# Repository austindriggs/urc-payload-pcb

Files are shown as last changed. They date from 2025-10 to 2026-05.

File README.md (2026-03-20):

# Payload PCB at WVU for Mars Society's University Rover Challenge (URC)







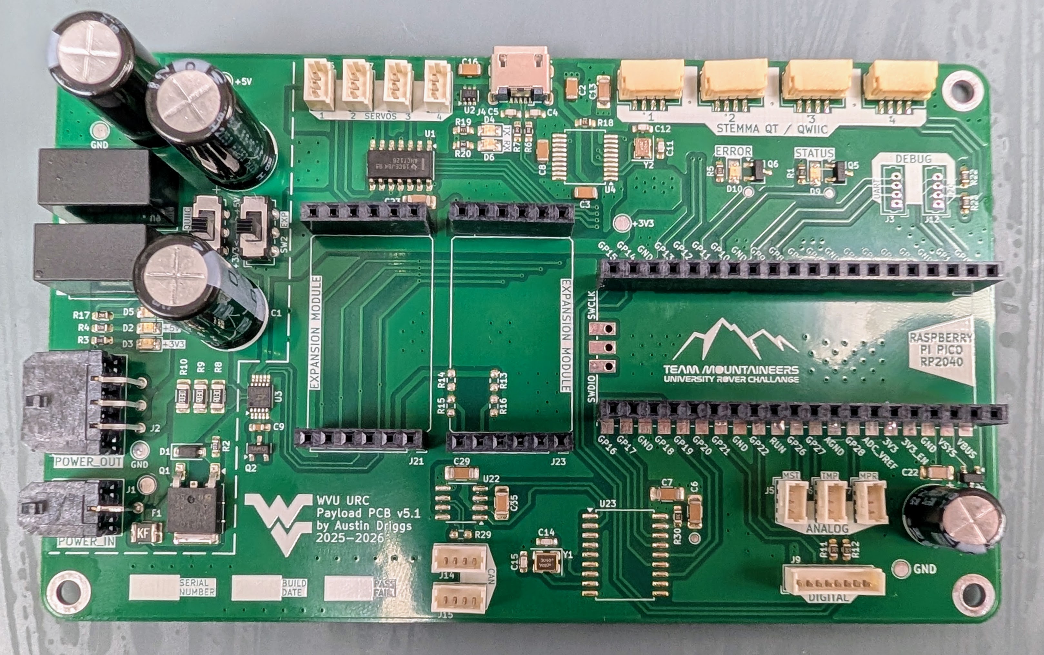
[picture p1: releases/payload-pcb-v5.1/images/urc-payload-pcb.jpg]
urc-payload-pcb


## SUMMARY

The Payload PCB serves as an all-purpose control and interface board that contains the Raspberry Pi Pico (RP2040) designed to manage mission-critical sensors and electronics and communicate that information through its Micro USB connector to the LattePanda Sigma SBC.

Learn how to [contribute](CONTRIBUTING.md) (with pictures) to this project.

## FEATURES

- Resettable PTC fuse and reverse voltage protection on +12V Molex Micro-Fit input.
- LTC2990 Quad I2C Voltage, Current, and Temperature Monitor.
- Traco TSR 2 Series +5V and +3V3 regulators: 96% eff, no heat sink required, built in filter caps, and short circuit protection.
- Outputs +12V, +5V, and +3V3 on Molex Micro-Fit.
- Status and error LEDs.
- Connections for both the Pico and an external device to CAN bus.
- 4x STEMMA QT / QWIIC connectors for COTS modules and peripherals.
- 2x custom expansion modules on two 6 pin 0.1" connectors each.
- 4x servo (PWM) outputs on Molex PicoBlades.
- 3x analog inputs on Molex Picoblades.
- 2x digital outputs for relays.
- 2x digital inputs (active-low) for limit switches on manipulator linear rail.
- Micro USB port with soft start to connect to Seeeduino XIAO on manipulator.

## DESIGN

<!--
### SCHEMATIC

TODO

### LAYOUT
--->

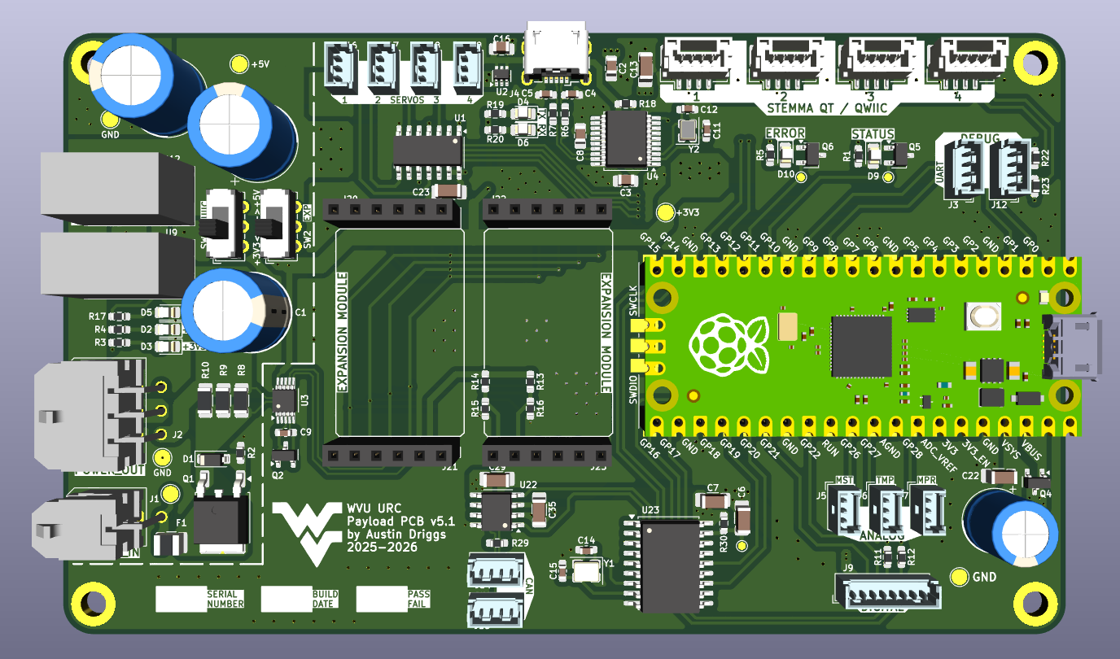
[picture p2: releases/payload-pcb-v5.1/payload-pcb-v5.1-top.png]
top


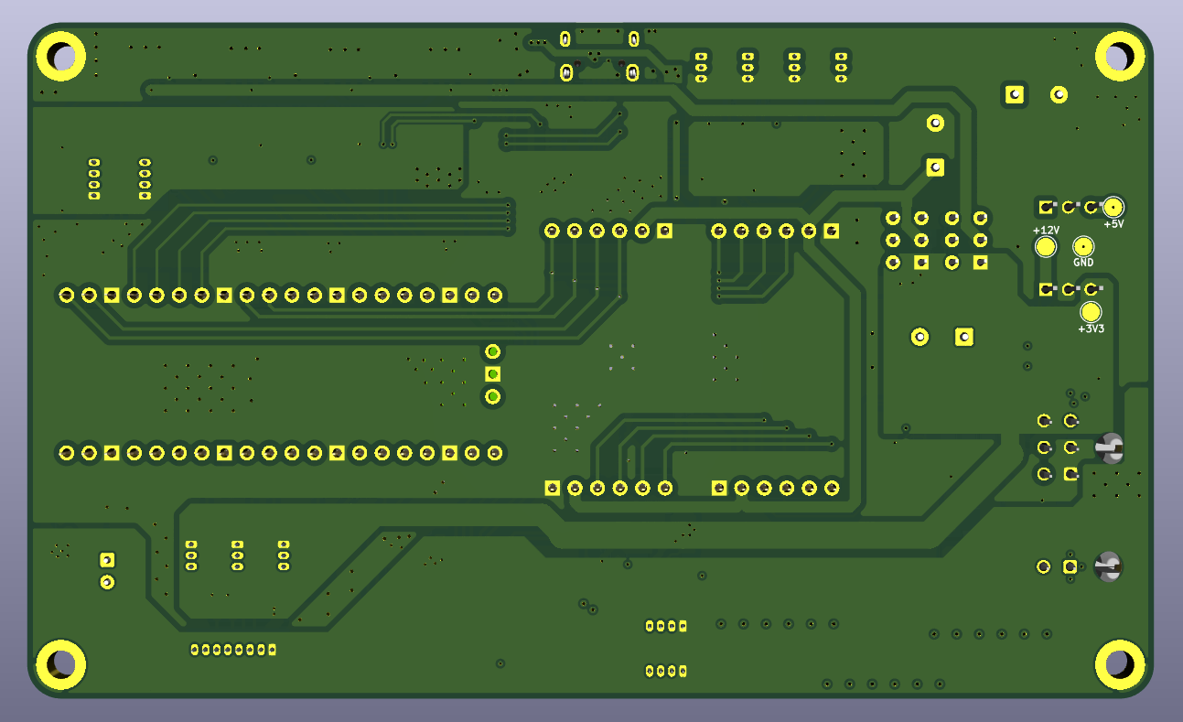
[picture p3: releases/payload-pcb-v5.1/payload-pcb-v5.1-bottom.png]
bottom


<!--
### MODEL

TODO
--->

## DEIMOS (ROVER) AND PHOBOS (DRONE) FOR 2026

Click the image below to watch the System Acceptance Review (SAR) on YouTube:  
<a href="https://youtu.be/ZTezlA8RuXI?si=s-GYmmxkBqftyrRB" target="_blank">
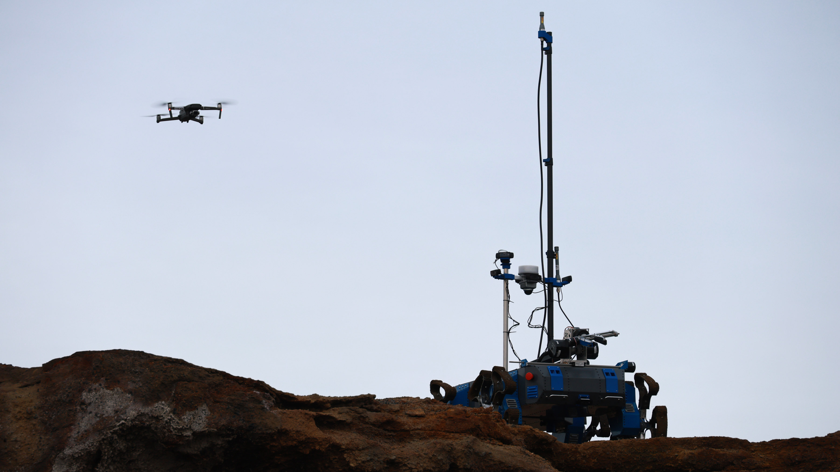
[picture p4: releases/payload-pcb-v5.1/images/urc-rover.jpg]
URC Rover Video
  
</a>

## LICENSE

This project is published under the MIT [license](LICENSE).

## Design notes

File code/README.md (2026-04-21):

# pico_interface_pkg

This package includes the code for both the node that needs to run on the Latte Panda to communicate with the pico as well as the code that needs to be flashed onto the pico.

The code on the pico itself has a simple overall function. It will poll its serial port, take in a message, and then decode that message and exectute an action based on its contents.

## starting

```bash
ros2 run pico_interface_pkg pico_host_node
```

## pico_science_node.py - (All Pico Code For Deimos)

Commands to run Linear Actuator on Manipulator

extend
```bash
ros2 topic pub --once /science/actuator_pos robot_interfaces/msg/STargetedFloat "{target: 'act', data: 1.0}"
```

retract
```bash
ros2 topic pub --once /science/actuator_pos robot_interfaces/msg/STargetedFloat "{target: 'act', data: 0.0}"
```

stop
```bash
ros2 topic pub --once /science/actuator_pos robot_interfaces/msg/STargetedFloat "{target: 'act', data: 0.5}"
```

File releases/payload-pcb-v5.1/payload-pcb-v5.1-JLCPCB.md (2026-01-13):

# Payload PCB v5.1 JLCPCB

The bolded text are what needs changed, but everything should be verified. Last updated: 2025-01-13

## Online PCB Quote

1. Add gerbers from `releases/payload-pcb-v5.1/gerbers/payload-pcb-v5.1-gerbers.zip`
2. Base Material = FR-4
3. **Layers = 4**
4. **Dimensions = 5 * 3 inch**
5. **PCB Qty = 10**
6. Product Type = Industrial/Consumer electronics

## PCB Specifications

1. Different Design = 1
2. Delivery Format = Single PCB
3. PCB Thickness = 1.6mm
4. **PCB Color = Blue**
5. Silkscreen = White
6. Material Type = FR4 TG135
7. Surface Finish = HASL (with lead)

## High-spec Options

1. Outer Copper Weight = 1 oz
2. Inner Copper Weight = 0.5 oz
3. **Specify Layer Sequence = Yes**
	1. L1 = F_Cu
	2. L2 = GND1
	3. L3 = GND2
	4. L4 = B_Cu
4. Specify Stackup = No
5. Via Covering = Tented
6. Via Plating Method = Not Specified
7. Min via hole size/diameter = 0.3mm
8. Board Outline Tolerance = +-0.2mm
9. Confirm Production file = no
10. Mark on PCB = Remove Mark
11. Electrical Test = Flying Probe Fully Test
12. Gold Fingers = No
13. Castellated Holes = No
14. Edge Plating = No
15. Blind Slots = No
16. UL Marking = No
17. Backdrill = No

## Stencil

1. Framwork = No
2. Step Stencil = No
3. Nano-Coating = No
4. Stencil Side = Top only
5. Dimensions = Standard Size = 380 * 280
6. Stencil Qty = 1
7. **Thickness = Select by Customer = 0.12 mm**
8. Stencil Process Type = Solder paste stencil
9. **Polishing Process = Etching**
10. Fiducials = No Fiducial
11. Confirm Production file = No
12. **Engrave Text = Yes = payload-pcb-v5.1**
13. Package Box = With JLCPCB logo

# Estimated Cost

## Charge Details

- Engineering fee $24.00
- Via Covering $0.00
- Surface Finish $0.00
- Color $4.90
- Board $10.10
- Stencil $7.00
- Engrave Text $0.49
- Etching $3.22

## PCB Build Time

-  **3-4 days $0.00**
-  3 days PCBA Only $0.00
-  2-3 days $64.30

## Calculated Price

- $49.71

## Shipping Estimate 

- $43.67
- DHL Express (DDP) 2-4 business days
- Weight 1.42kg

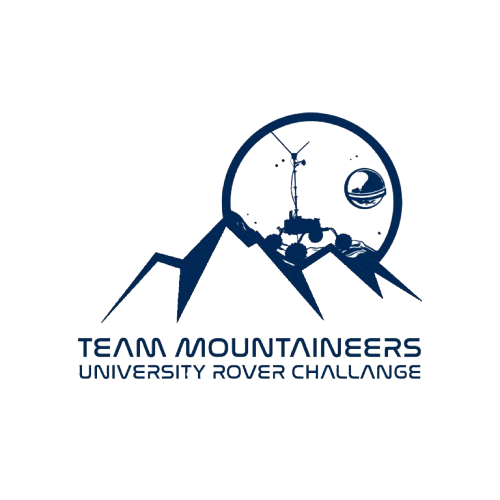
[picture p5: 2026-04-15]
support/Untitled design.png

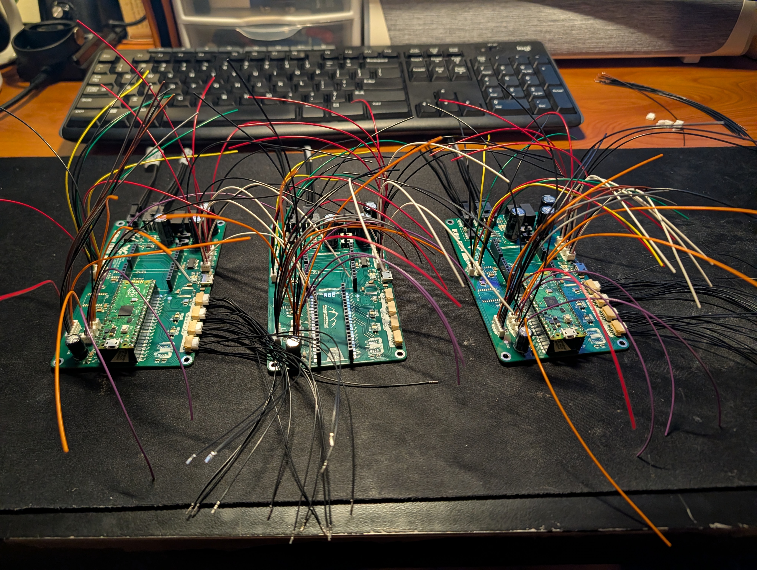
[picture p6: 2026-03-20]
releases/payload-pcb-v5.1/images/05-wired.jpg

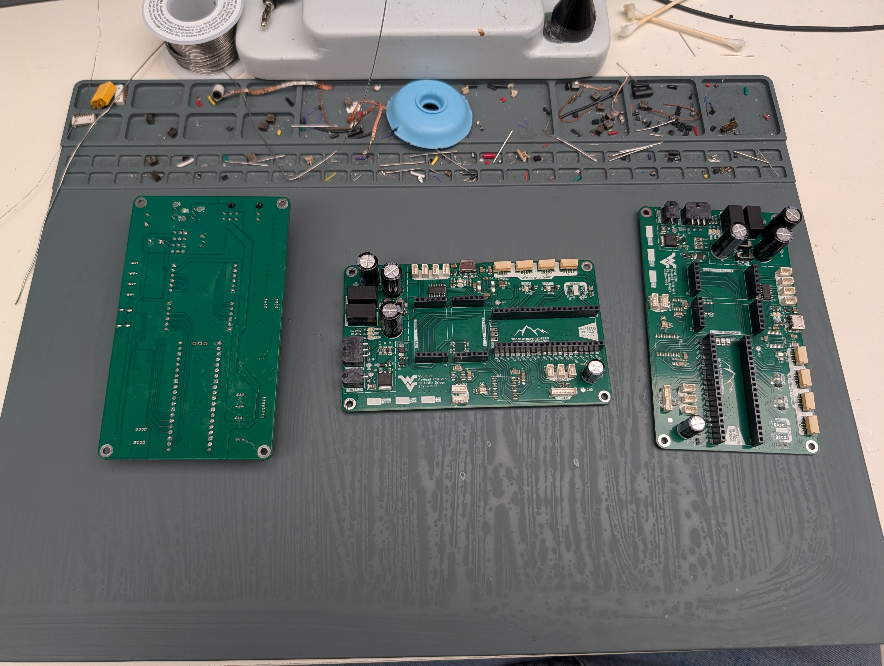
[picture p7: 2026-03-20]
releases/payload-pcb-v5.1/images/04-zoomed.jpg

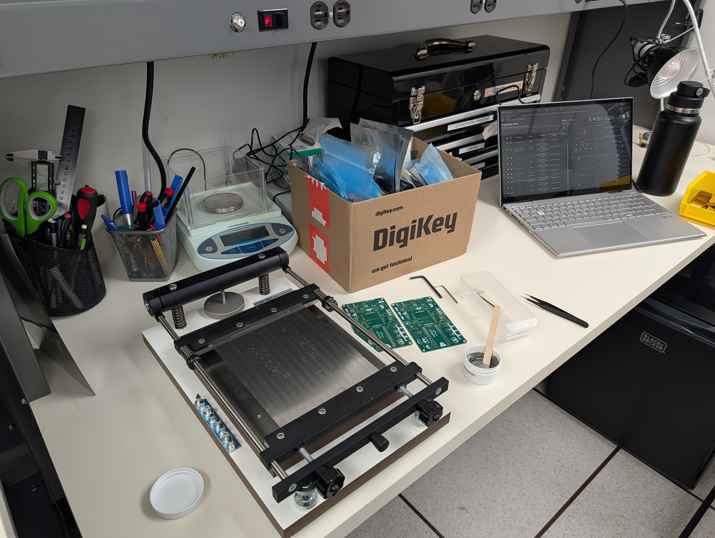
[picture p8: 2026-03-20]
releases/payload-pcb-v5.1/images/01-stencil.jpg

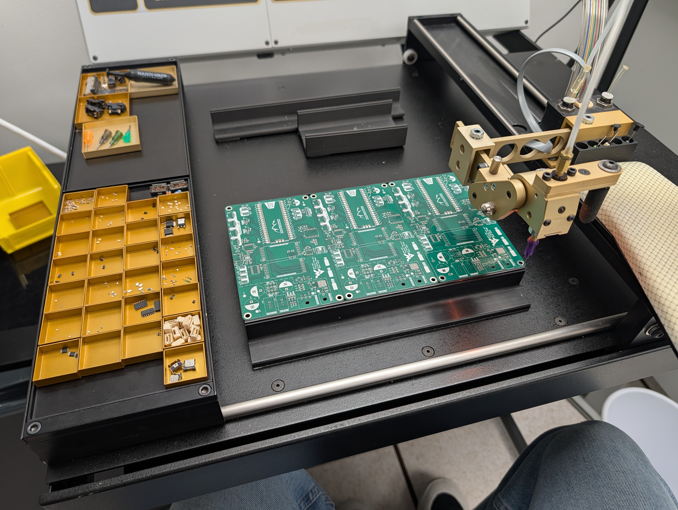
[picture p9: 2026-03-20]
releases/payload-pcb-v5.1/images/02-wiped.jpg

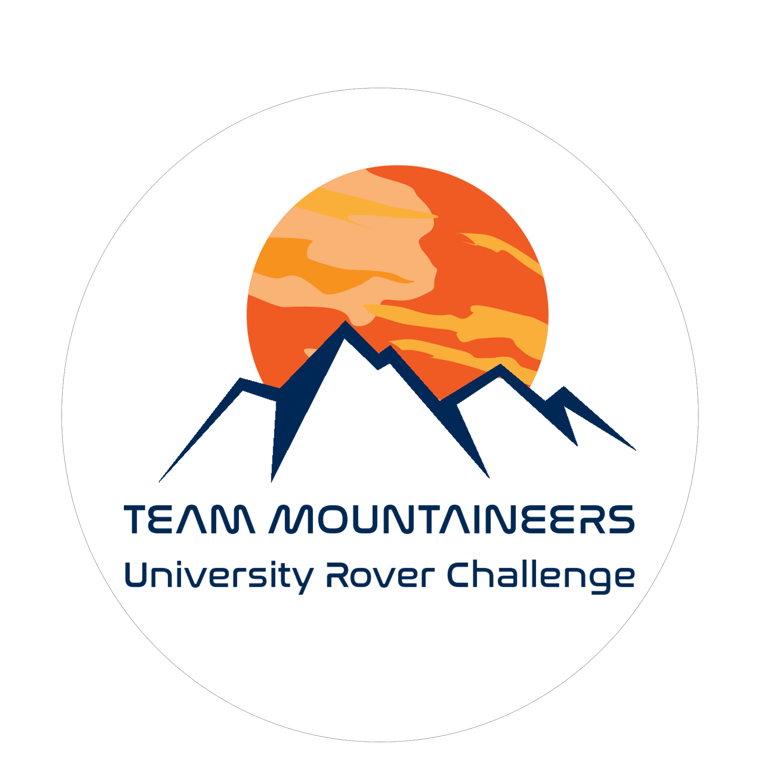
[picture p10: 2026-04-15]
support/urc_mars.png

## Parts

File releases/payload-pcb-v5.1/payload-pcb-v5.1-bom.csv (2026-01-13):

Reference | Value | DNP | Footprint | Datasheet | Description | Vendor | Vendor Part Number | Manufacturer | Manufacturer Part Number | Qty | Qty x5
C1,C10,C25 | 1000uF |  | Capacitor_THT:CP_Radial_D10.0mm_P5.00mm | https://www.nichicon.co.jp/english/series_items/catalog_pdf/e-uvr.pdf | CAP ALUM 1000UF 20% 25V RADIAL | Digikey | 493-1065-ND | Nichicon | UVR1E102MPD | 3 | 15
C2,C3,C6,C7,C8,C13,C16,C22,C23,C29,C35 | 0.1uF |  | Capacitor_SMD:C_0805_2012Metric_Pad1.18x1.45mm_HandSolder,Capacitor_SMD:C_1206_3216Metric_Pad1.33x1.80mm_HandSolder | https://www.yageogroup.com/content/datasheet/asset/file/KEM_C1002_X7R_SMD | CAP CER 0.1UF 50V X7R 1206 | Digikey | 399-C1206C104J5RACTUCT-ND | KEMET | C1206C104J5RACTU | 11 | 55
C4,C5 | 47p |  | Capacitor_SMD:C_0603_1608Metric_Pad1.08x0.95mm_HandSolder | https://www.yageogroup.com/content/datasheet/asset/file/KEM_C1002_X7R_SMD | CAP CER 47PF 50V X7R 0603 | Digikey | 399-C0603C470K5RACTUCT-ND | KEMET | C0603C470K5RACTU | 2 | 10
C9 | 470pF |  | Capacitor_SMD:C_0603_1608Metric_Pad1.08x0.95mm_HandSolder | https://www.yageogroup.com/content/datasheet/asset/file/KEM_C1002_X7R_SMD | CAP CER 470PF 50V X7R 0603 | Digikey | 399-C0603C471K5RACTUCT-ND | KEMET | C0603C471K5RACTU | 1 | 5
C11,C12,C14,C15 | 12pF |  | Capacitor_SMD:C_0603_1608Metric_Pad1.08x0.95mm_HandSolder | https://www.yageogroup.com/content/datasheet/asset/file/KEM_C1002_X7R_SMD | CAP CER 12PF 50V X7R 0603 | Digikey | 399-C0603C120K5RACTUCT-ND | KEMET | C0603C120K5RACTU | 4 | 20
C20 | 10uF |  | Capacitor_THT:CP_Radial_D8.0mm_P2.50mm | https://www.nichicon.co.jp/english/series_items/catalog_pdf/e-uvr.pdf | CAP ALUM 10UF 20% 160V RADIAL TH | Digikey | 493-12828-1-ND | Nichicon | UVR2C100MPD1TD | 1 | 5
D1 | BZT52C10-TP |  | Diode_SMD:D_SOD-123 | https://www.mccsemi.com/pdf/Products/BZT52C2V0_BZT52C75(500mW)(SOD-123).pdf | DIODE ZENER 10V 500MW SOD123 | Digikey | BZT52C10-TPMSCT-ND | MCC | BZT52C10-TP | 1 | 5
D2,D3,D4,D5,D6 | +12V,+3V3,+5V,RX,TX |  | LED_SMD:LED_0805_2012Metric_Pad1.15x1.40mm_HandSolder | https://www.we-online.com/components/products/datasheet/150080BS75000.pdf | LED GREEN CLEAR 0805 SMD | Digikey | 732-4983-1-ND | Würth Elektronik | 150080GS75000 | 5 | 25
D9 | STATUS |  | LED_SMD:LED_0805_2012Metric_Pad1.15x1.40mm_HandSolder | https://www.we-online.com/components/products/datasheet/150080BS75000.pdf | LED BLUE CLEAR 0805 SMD | Digikey | 732-4982-1-ND | Wurth Elektronik | 150080BS75000 | 1 | 5
D10 | ERROR |  | LED_SMD:LED_0805_2012Metric_Pad1.15x1.40mm_HandSolder | https://www.we-online.com/components/products/datasheet/150080BS75000.pdf | LED RED CLEAR 0805 SMD | Digikey | 732-4984-1-ND | Wurth Elektronik | 150080RS75000 | 1 | 5
F1 | PTC |  | Fuse:Fuse_1210_3225Metric | https://www.littelfuse.com/assetdocs/1210l-datasheet-update?assetguid=b3a2be92-83a1-491d-9c6d-dc64451de047 | PTC RESET FUSE 16V 1.5A 1210 | Digikey | F6135CT-ND | Littelfuse Inc. | 1210L150/16WR | 1 | 5
J1 | POWER_IN |  | Connector_Molex:Molex_Micro-Fit_3.0_43045-0200_2x01_P3.00mm_Horizontal | https://tools.molex.com/pdm_docs/ps/PS-43045.pdf | CONN HEADER R/A 2POS | Digikey | WM1813-ND | Molex | 430450200 | 1 | 5
J2 | POWER_OUT |  | Connector_Molex:Molex_Micro-Fit_3.0_43045-0600_2x03_P3.00mm_Horizontal | https://tools.molex.com/pdm_docs/ps/PS-43045.pdf | CONN HEADER R/A 6POS 3MM | Digikey | WM1821-ND | Molex | 430450602 | 1 | 5
J3,J12,J14,J15 | CAN,I2C,UART | DNP | Connector_Molex:Molex_PicoBlade_53047-0410_1x04_P1.25mm_Vertical | https://www.molex.com/pdm_docs/sd/530470310_sd.pdf | CONN HEADER VERT 4POS 1.25MM | Digikey | WM1733-ND | Molex | 530470410 | 4 | 20
J4 | USB |  | Connector_USB:USB_Micro-B_Wuerth_629105150521 | https://www.we-online.com/components/products/datasheet/629105150521.pdf | CONN RCPT USB2.0 MICRO B SMD R/A | Digikey | 732-5960-1-ND | Wurth Elektronik | 6.29105E+11 | 1 | 5
J5,J6,J7,J16,J17,J18,J19 | MANIPULATOR,MPR,MST,SCOOP,SERVO3,SERVO4,TMP |  | Connector_Molex:Molex_PicoBlade_53047-0310_1x03_P1.25mm_Vertical | https://www.molex.com/pdm_docs/sd/530470310_sd.pdf | CONN HEADER VERT 3POS 1.25MM | Digikey | WM1732-ND | Molex | 530470310 | 7 | 35
J8,J10,J11,J13 | QWIIC1,QWIIC2,QWIIC3,QWIIC4 |  | Connector_JST:JST_GH_BM04B-GHS-TBT_1x04-1MP_P1.25mm_Vertical | https://www.jst-mfg.com/product/pdf/eng/eGH.pdf | CONN HEADER SMD R/A 4POS 1.25MM | Digikey | 455-1566-1-ND | JST Sales America Inc. | SM04B-GHS-TB | 4 | 20
J9 | DIGITAL |  | Connector_Molex:Molex_PicoBlade_53047-0810_1x08_P1.25mm_Vertical | https://www.molex.com/pdm_docs/sd/530470310_sd.pdf | CONN HEADER VERT 8POS 1.25MM | Digikey | WM1737-ND | Molex | 530470810 | 1 | 5
J20,J21,J22,J23 | EXP1,EXP2,EXP3,EXP4 |  | Connector_PinSocket_2.54mm:PinSocket_1x06_P2.54mm_Vertical | https://mm.digikey.com/Volume0/opasdata/d220001/medias/docus/6129/ssw-1xx-xx-xxx-x-xx-xxx-xx-mkt.pdf | CONN RCPT 6POS 0.1 GOLD PCB | Digikey | SAM10025-ND | Samtec Inc. | SSW-106-01-F-S | 4 | 20
Q1 | SUD50P10-43L-GE3 |  | Package_TO_SOT_SMD:TO-252-2 | https://www.vishay.com/docs/73444/sud50p10.pdf | MOSFET P-CH 100V 37.1A TO252 | Digikey | SUD50P10-43L-GE3CT-ND | Vishay Siliconix | SUD50P10-43L-GE3 | 1 | 5
Q2 | MMBT3904 |  | Package_TO_SOT_SMD:SOT-23 | https://www.onsemi.com/pdf/datasheet/mmbt3904lt1-d.pdf | TRANS NPN 40V 0.2A SOT23-3 | Digikey | MMBT3904LT1GOSCT-ND | onsemi | MMBT3904LT1G | 1 | 5
Q4 | DMG2305UX |  | Package_TO_SOT_SMD:SOT-23 | https://www.diodes.com/assets/Datasheets/DMG2305UX.pdf | MOSFET P-CH 20V 4.2A SOT23 | Digikey | DMG2305UX-7DICT-ND | Diodes Incorporated | DMG2305UX-7 | 1 | 5
Q5,Q6 | 2N7002 |  | Package_TO_SOT_SMD:TSOT-23 | https://www.onsemi.com/download/data-sheet/pdf/nds7002a-d.pdf | MOSFET SOT23 N 60V 5OHM 150C | Digikey | 2N7002NCT-ND | onsemi | 2N7002 | 2 | 10
R1,R3,R6,R7,R20 | 22 |  | Resistor_SMD:R_0603_1608Metric_Pad0.98x0.95mm_HandSolder | https://www.seielect.com/catalog/SEI-RNCP.pdf | RES 22.1 OHM 1% 1/8W 0603 | Digikey | RNCP0603FTD22R1CT-ND | Stackpole Electronics Inc | RNCP0603FTD22R1 | 5 | 25
R2 | 100k |  | Resistor_SMD:R_0603_1608Metric_Pad0.98x0.95mm_HandSolder | https://www.seielect.com/catalog/SEI-RMCF_RMCP.pdf | RES 100K OHM 1% 1/10W 0603 | Digikey | RMCF0603FT100KCT-ND | Stackpole Electronics Inc | RMCF0603FT100K | 1 | 5
R4,R5,R19 | 330 |  | Resistor_SMD:R_0603_1608Metric_Pad0.98x0.95mm_HandSolder | https://www.seielect.com/catalog/SEI-RNCP.pdf | RES 332 OHM 1% 1/8W 0603 | Digikey | RNCP0603FTD332RCT-ND | Stackpole Electronics Inc | RNCP0603FTD332R | 3 | 15
R8,R9,R10 | 30m |  | Resistor_SMD:R_1206_3216Metric_Pad1.30x1.75mm_HandSolder | https://www.seielect.com/catalog/SEI-CSR_CSRN.pdf | RES 0.03 OHM 1% 1/2W 1206 | Digikey | 738-CSR1206FT30L0CT-ND | Stackpole Electronics Inc | CSR1206FT30L0 | 3 | 15
R11,R12,R13,R14,R15,R16,R18,R30 | 10k | DNP | Resistor_SMD:R_0603_1608Metric_Pad0.98x0.95mm_HandSolder | https://www.seielect.com/catalog/SEI-RNCP.pdf | RES 10K OHM 1% 1/8W 0603 | Digikey | RNCP0603FTD10K0CT-ND | Stackpole Electronics Inc | RNCP0603FTD10K0 | 8 | 40
R17 | 1k78 |  | Resistor_SMD:R_0603_1608Metric_Pad0.98x0.95mm_HandSolder | https://www.seielect.com/catalog/SEI-RNCP.pdf | RES 1.78K OHM 1% 1/8W 0603 | Digikey | RNCP0603FTD1K78CT-ND | Stackpole Electronics Inc | RNCP0603FTD1K78 | 1 | 5
R22,R23 | 3k3 |  | Resistor_SMD:R_0603_1608Metric_Pad0.98x0.95mm_HandSolder | https://www.seielect.com/catalog/SEI-RNCP.pdf | RES 3.3K OHM 1% 1/8W 0603 | Digikey | 738-RNCP0603FTD3K30CT-ND | Stackpole Electronics Inc | RNCP0603FTD3K30 | 2 | 10
R29 | 120 | DNP | Resistor_SMD:R_0603_1608Metric_Pad0.98x0.95mm_HandSolder | https://www.seielect.com/catalog/SEI-RNCP.pdf | RES 121 OHM 1% 1/8W 0603 | Digikey | RNCP0603FTD121RCT-ND | Stackpole Electronics Inc | RNCP0603FTD121R | 1 | 5
SW1,SW2 | EXP,QUIIC |  | Button_Switch_THT:SW_E-Switch_EG1271_SPDT | https://configured-product-images.s3.amazonaws.com/Datasheets/EG.pdf | SWITCH SLIDE SPDT 300MA 30V | Digikey | EG1919-ND | E-Switch | EG1271A | 2 | 10
U1 | SN74AHCT126DR |  | Package_SO:SOIC-14_3.9x8.7mm_P1.27mm | https://www.ti.com/general/docs/suppproductinfo.tsp?distId=10 | IC BUFF NON-INVERT 5.5V 14-SOIC | Digikey | 296-4658-1-ND | Texas Instruments | SN74AHCT126DR | 1 | 5
U2 | MIC94093YC6 |  | Package_TO_SOT_SMD:SOT-363_SC-70-6 | https://ww1.microchip.com/downloads/aemDocuments/documents/OTH/ProductDocuments/DataSheets/mic9409x.pdf | IC PWR SWITCH P-CHAN 1:1 SC70-6 | Digikey | 576-3490-1-ND | Microchip Technology | MIC94093YC6-TR | 1 | 5
U3 | LTC2990 |  | Package_SO:MSOP-10_3x3mm_P0.5mm | https://www.analog.com/media/en/technical-documentation/data-sheets/ltc2990.pdf | IC TEMP/VOLT/CUR MONITOR 10MSOP | Digikey | 505-LTC2990IMS#TRPBFCT-ND | Analog Devices Inc. | LTC2990IMS#TRPBF | 1 | 5
U4 | MCP2200 |  | Package_SO:SSOP-20_5.3x7.2mm_P0.65mm | http://ww1.microchip.com/downloads/en/DeviceDoc/200022228D.pdf | USB 2.0 TO UART PROTOCOL CONVERT | Digikey | MCP2200T-E/SS | Microchip Technology | 150-MCP2200T-E/SSCT-ND | 1 | 5
U9 | +5V@2A |  | footprints:TSR_2-24xx | https://www.tracopower.com/products/tsr2.pdf | DC DC CONVERTER 5V 10W | Digikey | 1951-2692-ND | Traco Power | TSR 2-2450 | 1 | 5
U12 | +3V3@2A |  | footprints:TSR_2-24xx | https://www.tracopower.com/products/tsr2.pdf | DC DC CONVERTER 3.3V 6.6W | Digikey | 1951-2426-ND | Traco Power | TSR 2-2433 | 1 | 5
U14 | PI_PICO |  | footprints:RPi_Pico_SMD_TH | https://datasheets.raspberrypi.com/pico/pico-datasheet.pdf | RASPBERRY PI PICO RP2040 | Digikey | 2648-SC0915CT-ND | Raspberry Pi | SC0915 | 1 | 5
U22 | MCP2562 |  | Package_SO:SOIC-8_3.9x4.9mm_P1.27mm | https://ww1.microchip.com/downloads/en/DeviceDoc/20005284A.pdf | IC TRANSCEIVER 1/1 8SOIC | Digikey | MCP2562FDT-E/SNCT-ND | Microchip Technology | MCP2562FDT-E/SN | 1 | 5
U23 | MCP2515 |  | Package_SO:SOIC-18W_7.5x11.6mm_P1.27mm | https://ww1.microchip.com/downloads/en/DeviceDoc/MCP2515-Stand-Alone-CAN-Controller-with-SPI-20001801J.pdf | IC CAN CONTROLLER W/SPI 18SOIC | Digikey | MCP2515T-E/SOCT-ND | Microchip Technology | MCP2515T-E/SO | 1 | 5
Y1 | 8MHz |  | Crystal:Crystal_SMD_3225-4Pin_3.2x2.5mm | https://www.diodes.com/assets/Datasheets/FH.pdf | CRYSTAL 8.0000MHZ 12PF SMD | Digikey | FL0800011QDICT-ND | Diodes Incorporated | FL0800011Q | 1 | 5
Y2 | 12MHz |  | Crystal:Crystal_SMD_2520-4Pin_2.5x2.0mm | https://www.diodes.com/assets/Datasheets/FH.pdf | CRYSTAL 12.0000MHZ 12PF SMD | Digikey | FH1200004CT-ND | Diodes Incorporated | FH1200004 | 1 | 5

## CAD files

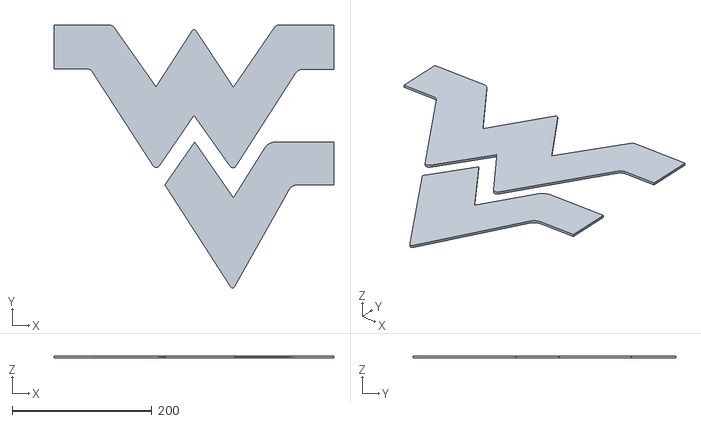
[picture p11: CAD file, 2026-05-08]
support/flying_wv.stl
400.0 x 376.0 x 3.00

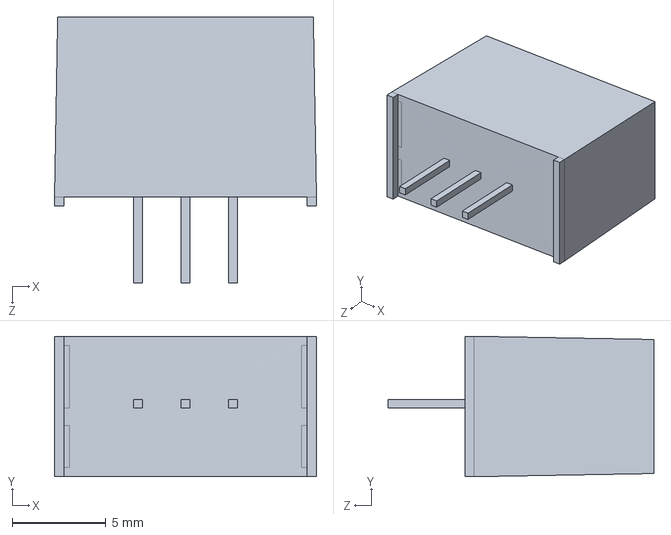
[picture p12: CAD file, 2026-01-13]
models/TSR-2-2450.stp
14.0 x 7.50 x 14.2 mm

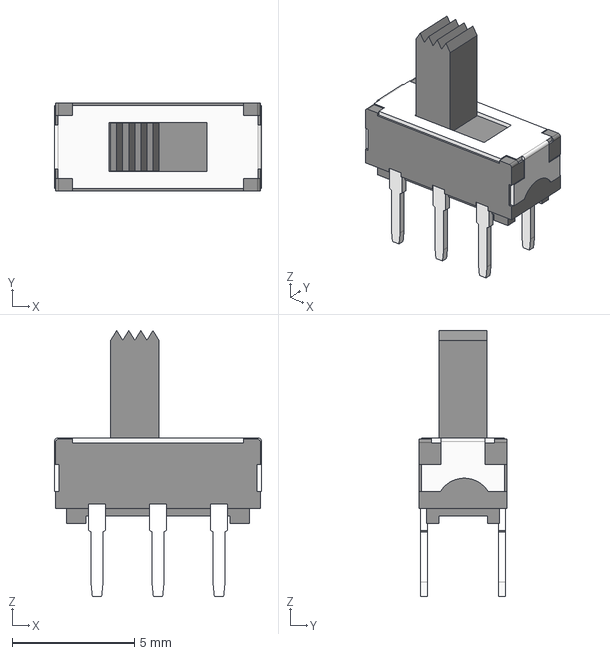
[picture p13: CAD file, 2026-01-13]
models/EG1271A.stp
8.50 x 3.60 x 10.9 mm

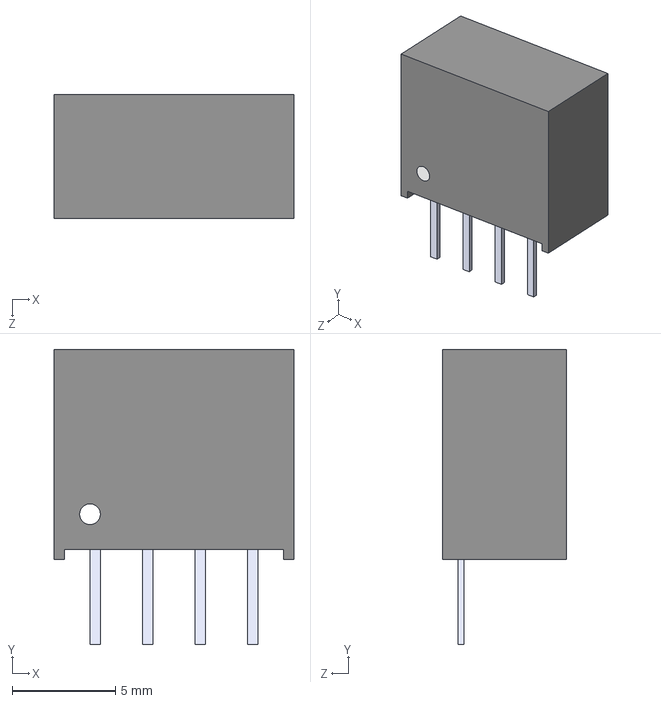
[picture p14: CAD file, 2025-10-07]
models/B0505S-1WR3.step
11.6 x 14.3 x 6.00 mm

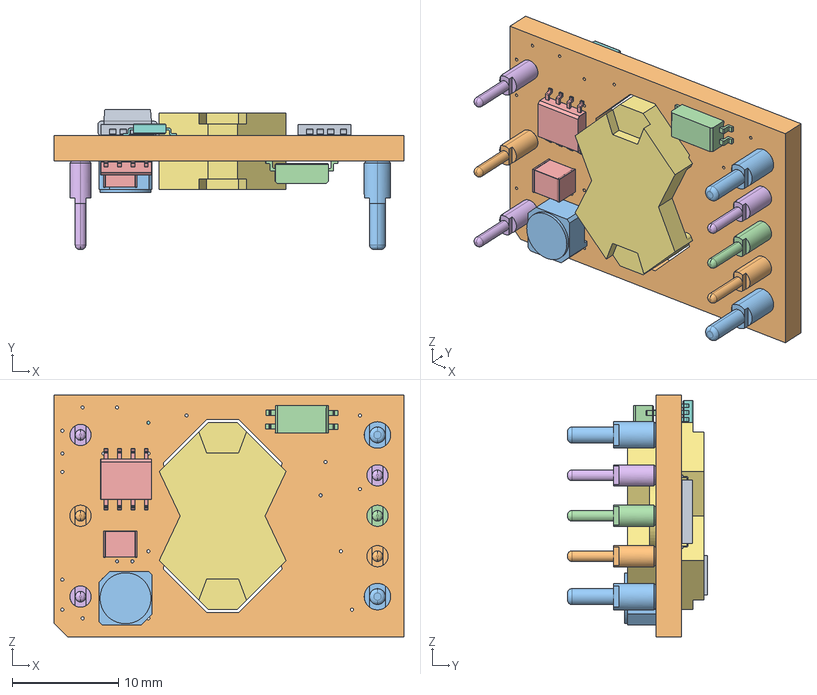
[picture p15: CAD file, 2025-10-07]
models/Sixteenth_Brick_Module.STEP
33.0 x 13.2 x 22.8 mm

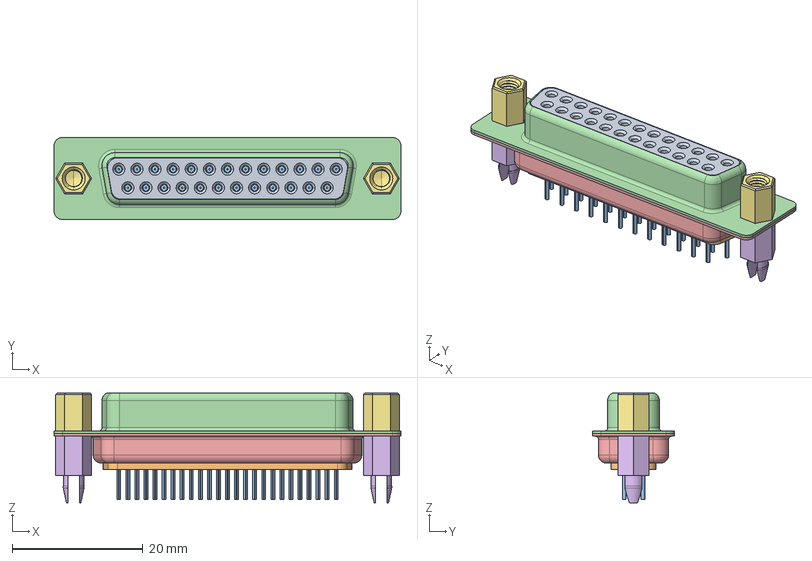
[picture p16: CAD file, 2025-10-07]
models/L77SDBH25SOL2RM8.STEP
53.0 x 12.6 x 16.8 mm
25PIN-FRONT-HOUSING-FEMALE
25PIN-BACK-HOUSING-FEMALE
TERMINAL-FEMALE-100SERIES x 25
101-25FEMALE-FRONTSHELL
101-25FEMALE-BACKSHELL

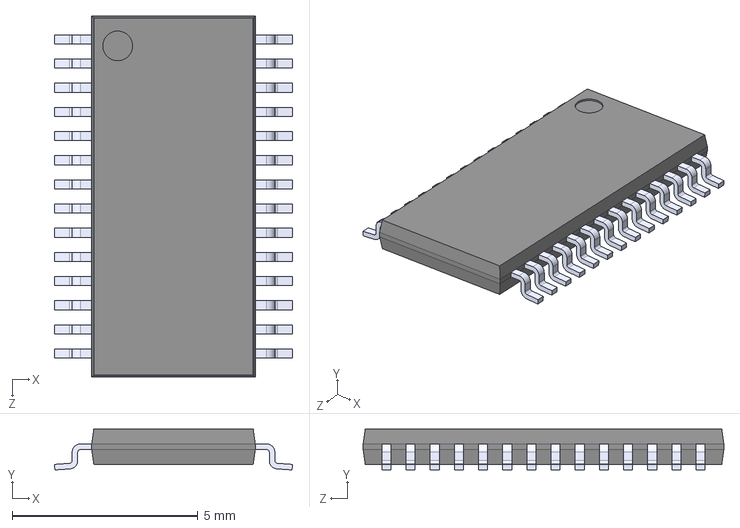
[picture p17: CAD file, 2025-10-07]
models/PCA9685PW_118.step
6.40 x 1.10 x 9.70 mm

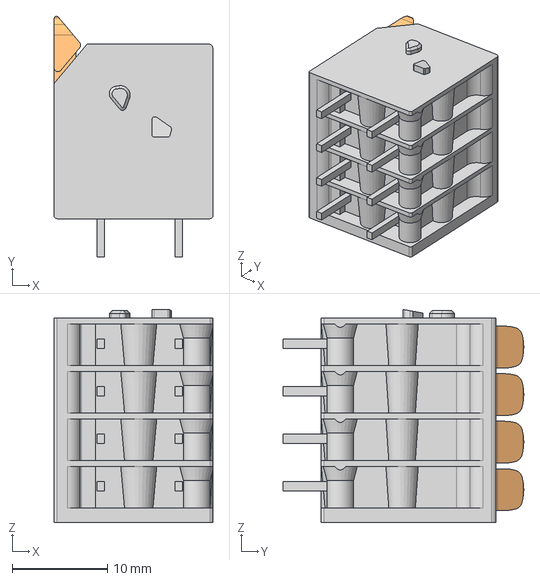
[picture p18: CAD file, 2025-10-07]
models/2604-3104.stp
16.7 x 25.3 x 22.4 mm

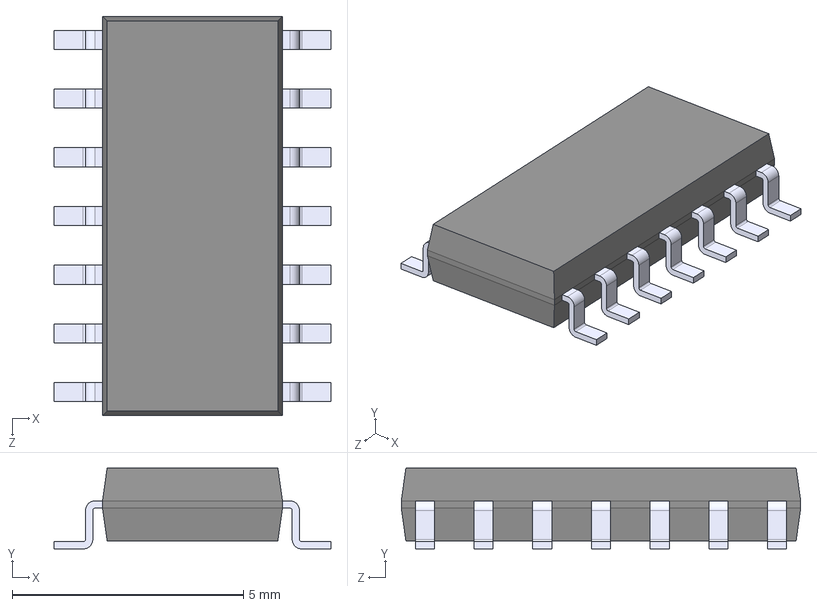
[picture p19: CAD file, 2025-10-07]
models/MCP3428-E_SL.step
5.99 x 1.75 x 8.65 mm

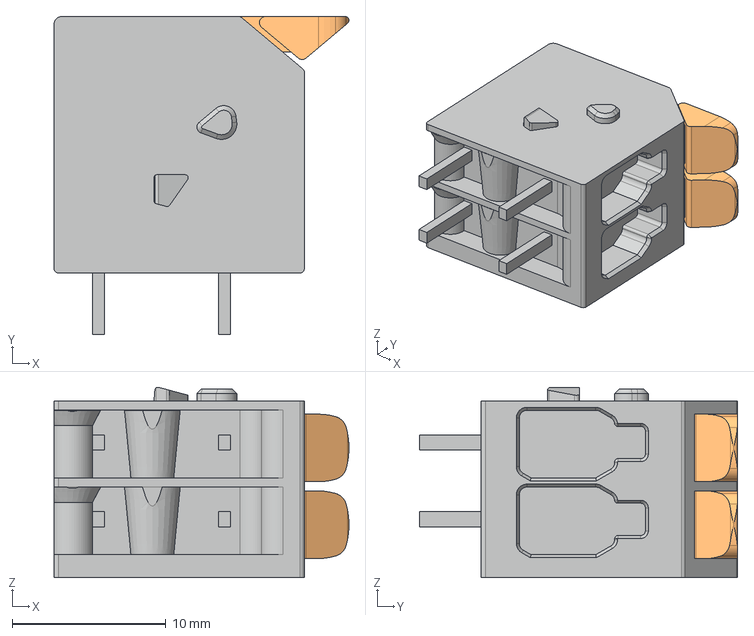
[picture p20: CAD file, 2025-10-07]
models/2604-1102.stp
19.2 x 20.7 x 12.4 mm

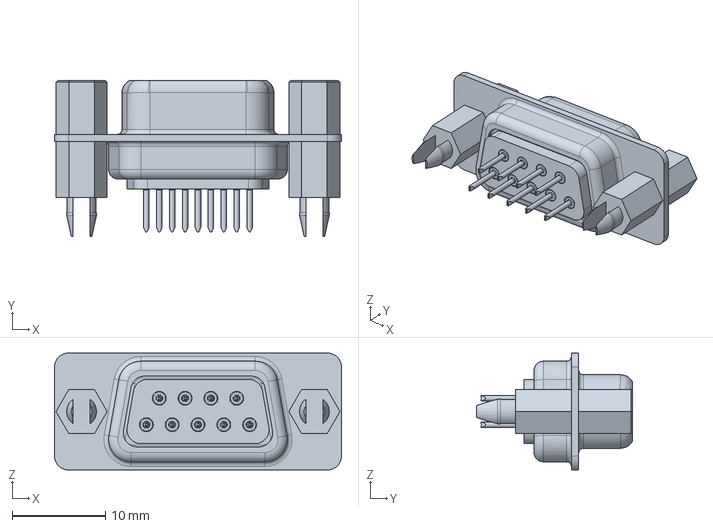
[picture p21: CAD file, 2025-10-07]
models/L77SDEH09SOL2RM8.stp
30.8 x 16.8 x 12.6 mm

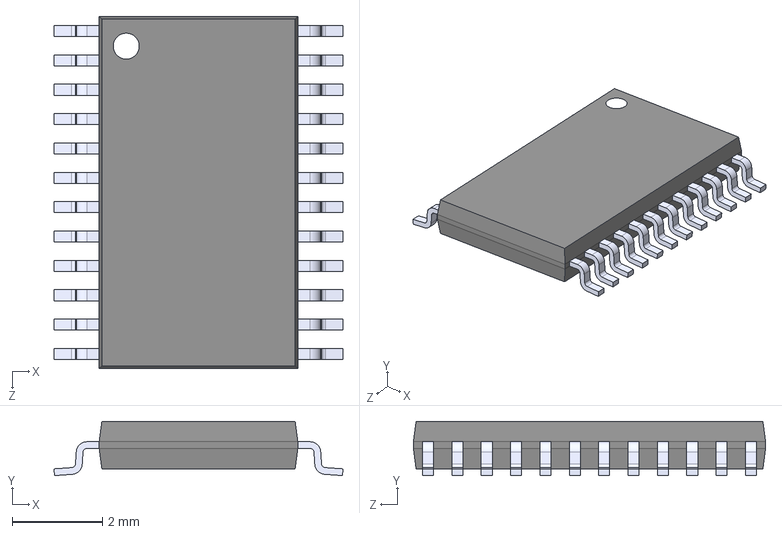
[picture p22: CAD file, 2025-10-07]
models/PCA9555PWR.step
6.40 x 1.20 x 7.80 mm

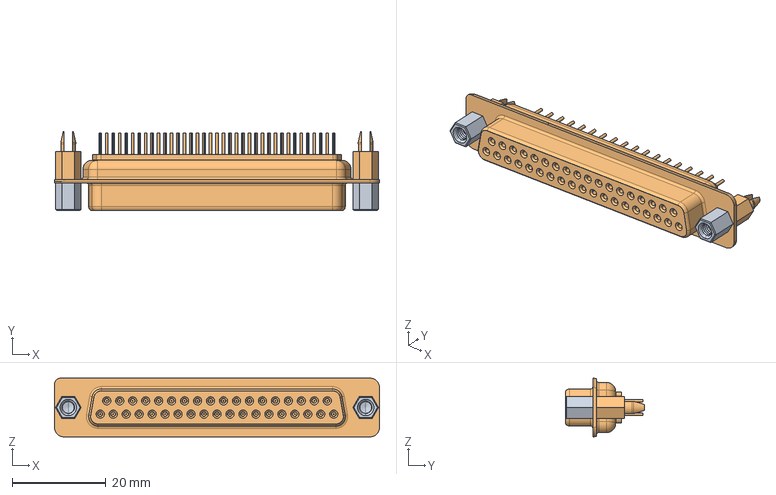
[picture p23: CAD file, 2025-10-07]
models/L77SDCH37SOL2RM8.STEP
69.4 x 16.8 x 12.6 mm

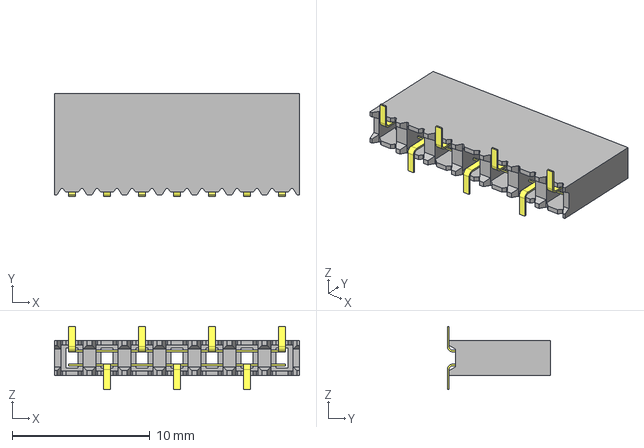
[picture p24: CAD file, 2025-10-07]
models/SSM-107-L-SV-BE.stp
17.8 x 7.49 x 4.57 mm
C-95-027
SSM-107-L-SV-BE_body

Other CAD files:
models/ROB-14450.step
models/DRV8874_carrier.step
models/TSW-106-07-S-T.stp
models/050362296.stp
models/1050170001.stp
models/173010342_STP_173010342_rev1.stp
models/39301062.STEP
models/39301062.stp
models/393570002.stp
models/395000004.stp
models/395011004.stp
models/430450200.stp
models/430450400.stp
models/430450602.stp
models/469911024.stp
models/530470310.stp
models/530470410.stp
models/530470810.stp
models/530480260.stp
models/530480410.step
models/530480610.stp
models/622-015-260-042 - EDAC D-Sub Connector.STEP
models/629105150521.stp
models/768250002.stp
models/768250004.stp
models/768250008.stp
models/768290102.stp
models/CAPC340180_88N_KEM.step
models/CAP_CK06_AVX.step
models/CAP_MA1812_C_MTK.step
models/CAP_UCD_5X5P8_NCH.step
models/DF3-4P-2DS.stp
models/HTSSOP16_STM.step
models/ISO1050DUBR.step
models/Pico.skp
models/TSW-104-07-T-T.step
models/TSW-105-08-G-T-RA.stp
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

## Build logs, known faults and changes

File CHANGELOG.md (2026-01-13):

# CHANGE LOG

## v5.1

Description: Continued revision after PDR and general suggestions. Uses the Raspberry Pi Pico as well as QWIIC and custom expansion modules.
Status: FABRICATION
Date: 2026-01-03
Release: [link](releases/payload-pcb-v5.1/) to files and gerbers.
Rover: TBD-2026
KiCad: 9.0.4
Contributors: Austin Driggs (ard00029@mix.wvu.edu)
Issues: No known issues.

Changes:
- Board size changed to 3 x 5 inches.
- Added STEMMA QT / QWIIC connectors.
- Added custom expansion module connectors.
- Added USB connector to try and connect to the Seeeduino XIAO. (experimental)
- Routed board and added silkscreen elements.
- Updated BOM, notes, and documentation.
- Swapped UART-to-USB from FTDI (out of stock) to MCP2200.

## v5.0

Description: Major rework to support the 2026 rover using a Raspberry Pi Pico.
Status: This board was never routed or fabbed.
Date: 2025-12-04
Rover: TBD-2026
KiCad: 9.0.4
Issues: See status.

Changes:
- Major repo cleanup and reorganization.
- Board size changed to 2.5 x 4 inches.
- General layout placement and planning.

## v4.0

Description: This was never fabbed. It swapped the Pi Pico for the Teensy.

## v3.1

Description: Iteration of the payload PCB used on the 2023 robot.

## v3.0

Description: Third iteration of the payload PCB, revised to use a Raspberry Pi Pico.

## v2.0

Description: Revised version of the payload PCB, compatible with Arduino Mega.

## v1.0

Description: The first version of the payload PCB, compatible with an Arduino Mega.

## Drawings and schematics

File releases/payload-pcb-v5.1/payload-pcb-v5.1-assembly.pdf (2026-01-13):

J21 | D4 1 | 2 | 3 | 4 | 5 | 6

A

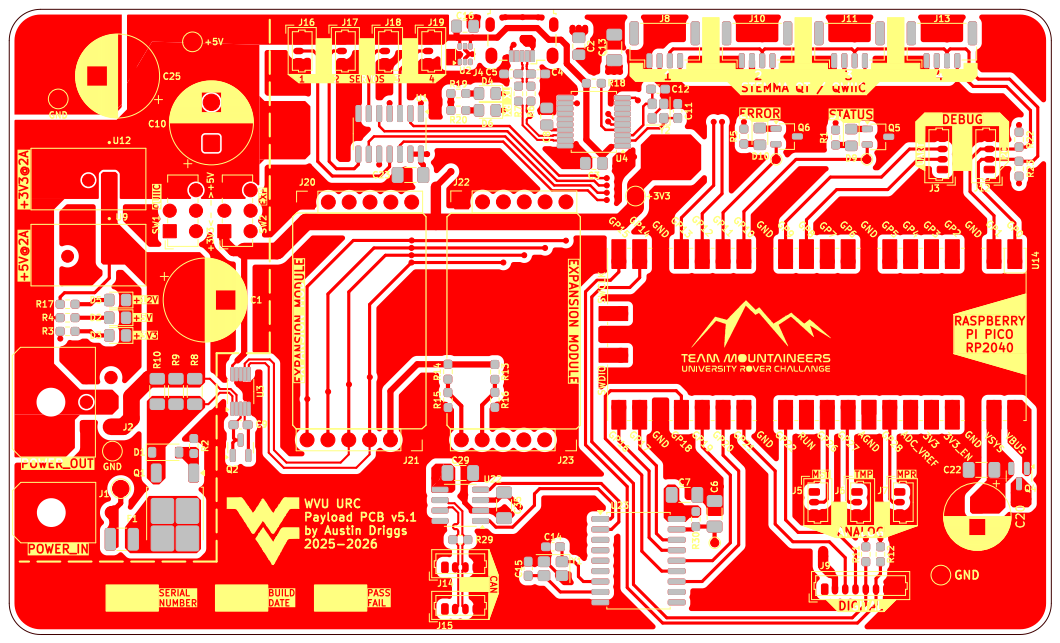
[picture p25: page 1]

WVU URC
Payload PCB v5.1 by Austin Driggs

File: payload-pcb.kicad_pcb Sheet: Front Copper WVU Unviersity Rover Challenge (URC) Front Copper - Page 1/3

Id: /1 Title: Payload PCB

A

A

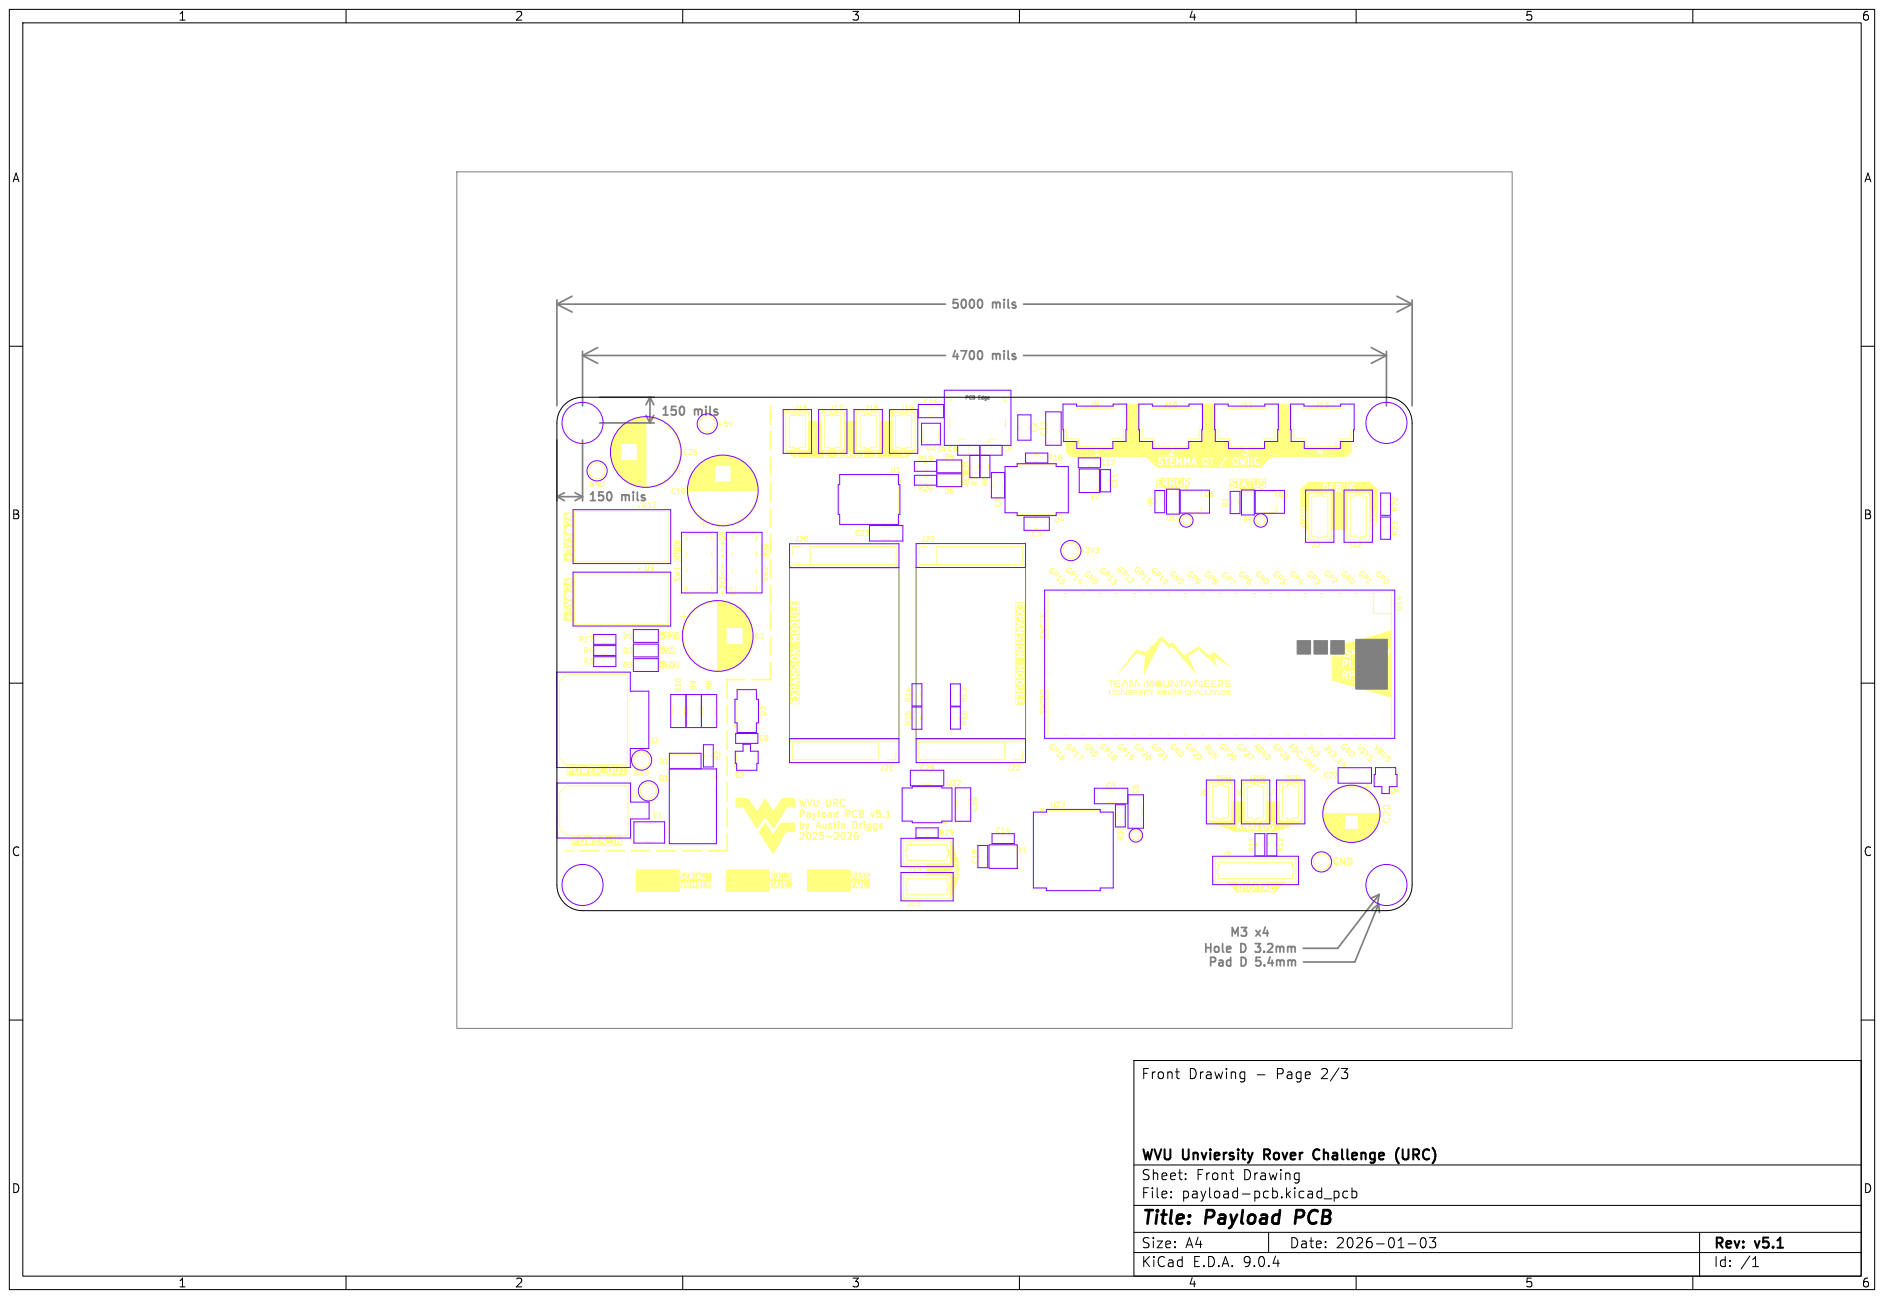
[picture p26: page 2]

WVU URC
Payload PCB v5.1 by Austin Driggs

File: payload-pcb.kicad_pcb Sheet: Front Drawing WVU Unviersity Rover Challenge (URC) Front Drawing - Page 2/3

Id: /1 Title: Payload PCB

A

A

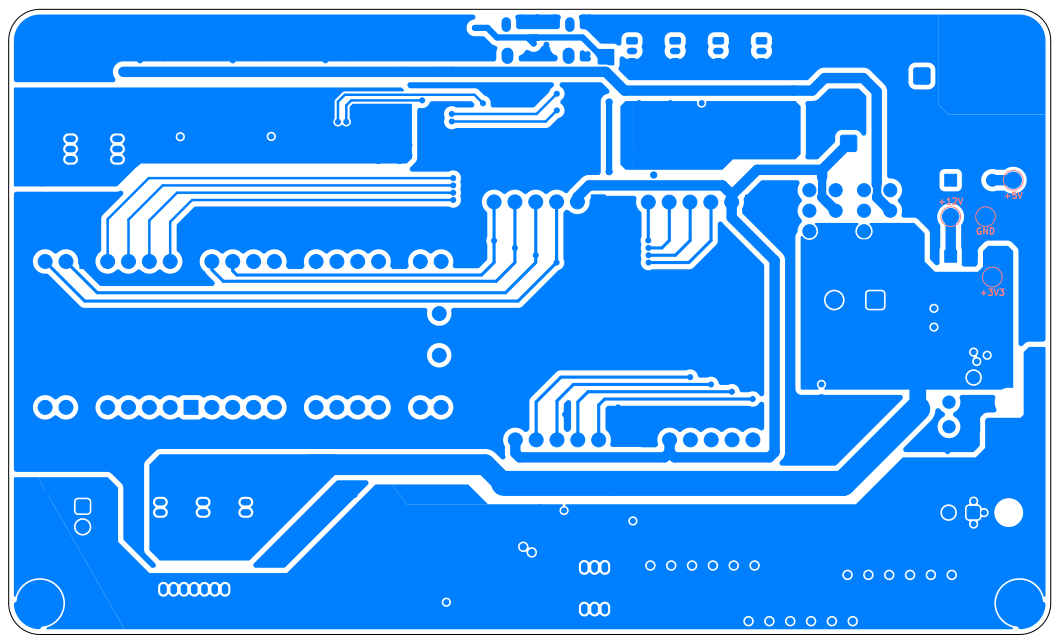
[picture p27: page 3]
GND; D Date: 2026-01-03 KiCad; E.D.A. 9.0.4 Size: A4; Rev: v5.1; File: payload-pcb.kicad_pcb Sheet: Back Copper WVU Unviersity; Rover Challenge (URC) Back; Copper -; Page 3/3

Id: /1 Title: Payload PCB

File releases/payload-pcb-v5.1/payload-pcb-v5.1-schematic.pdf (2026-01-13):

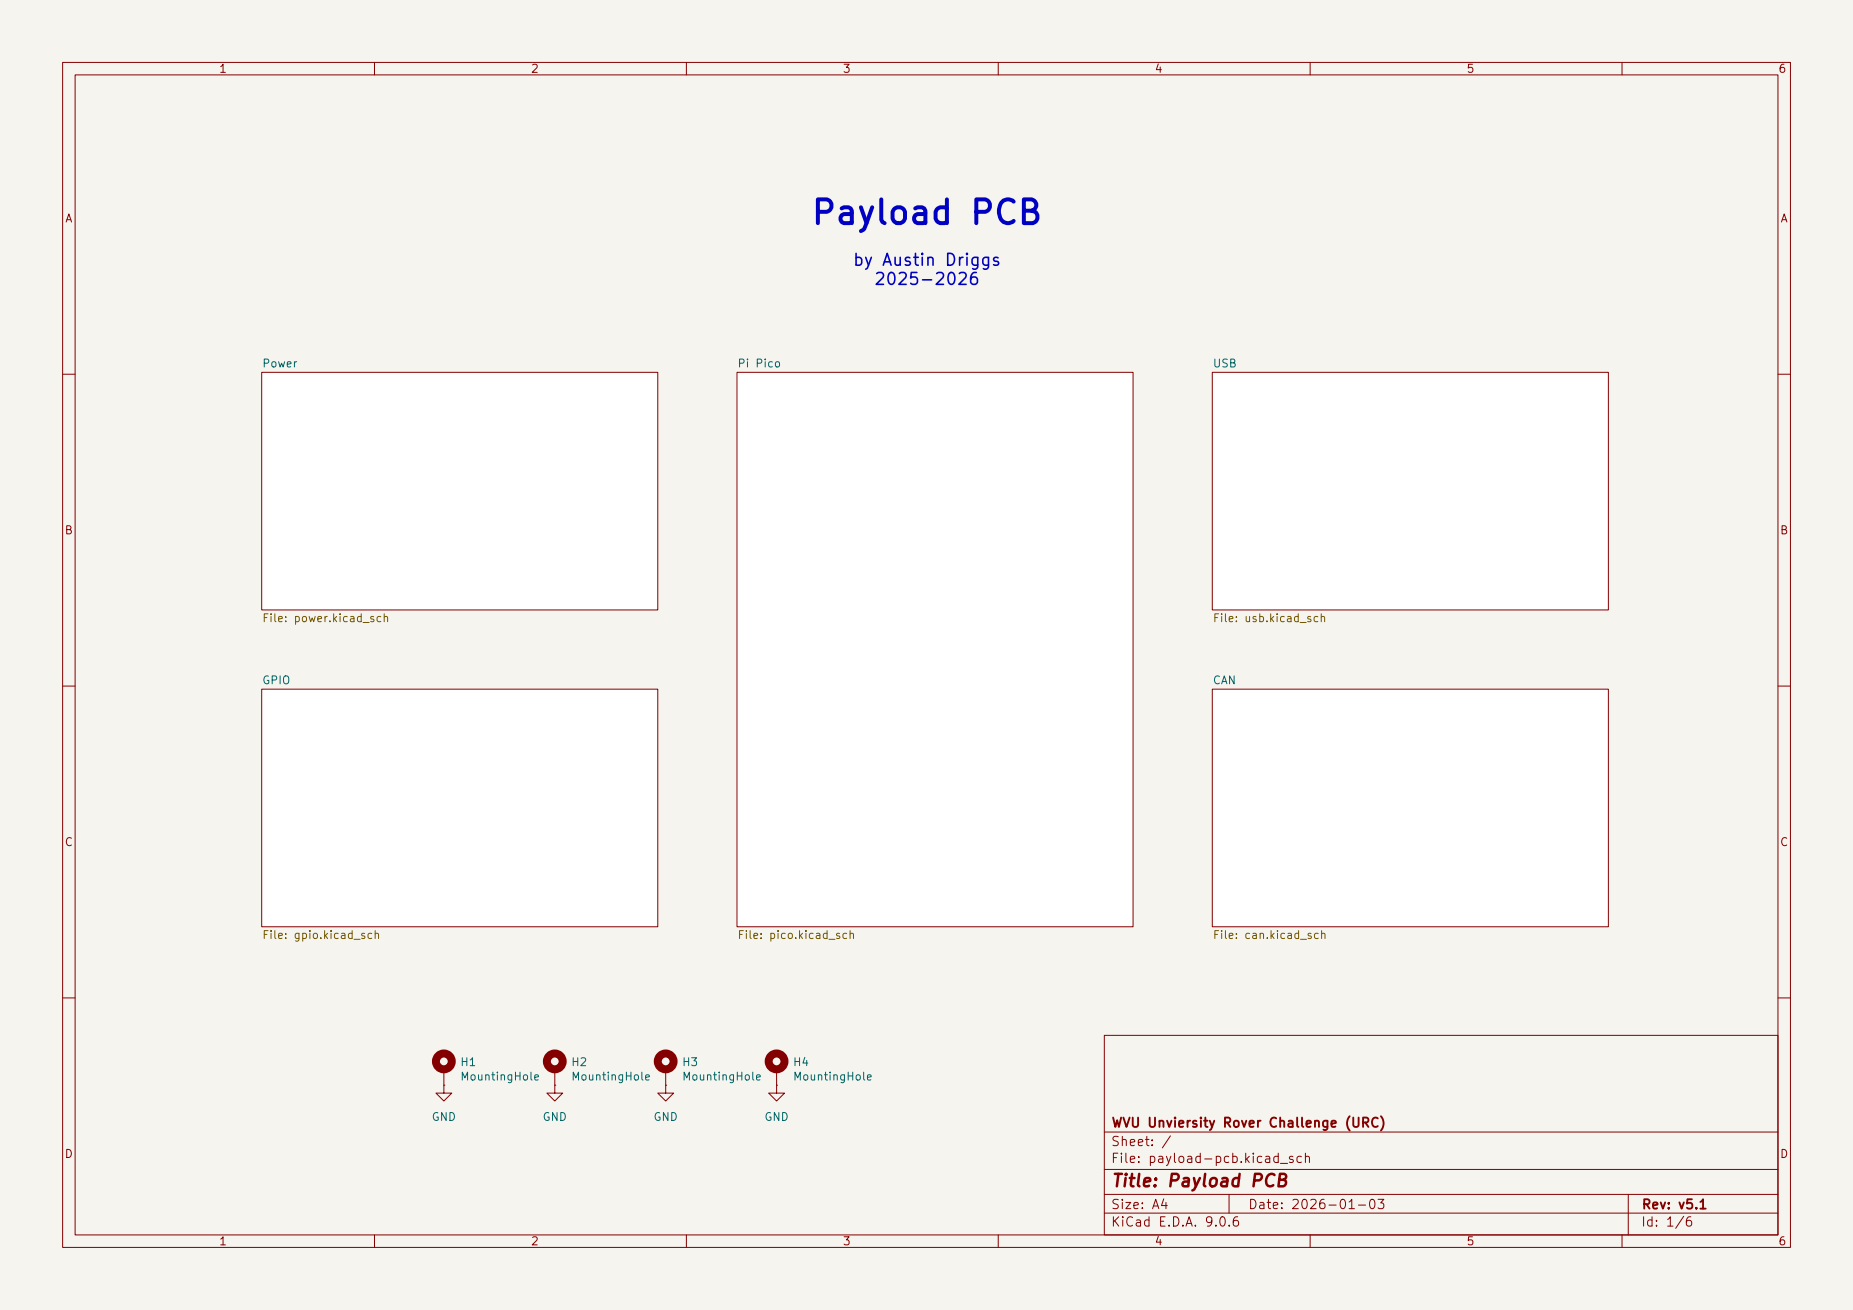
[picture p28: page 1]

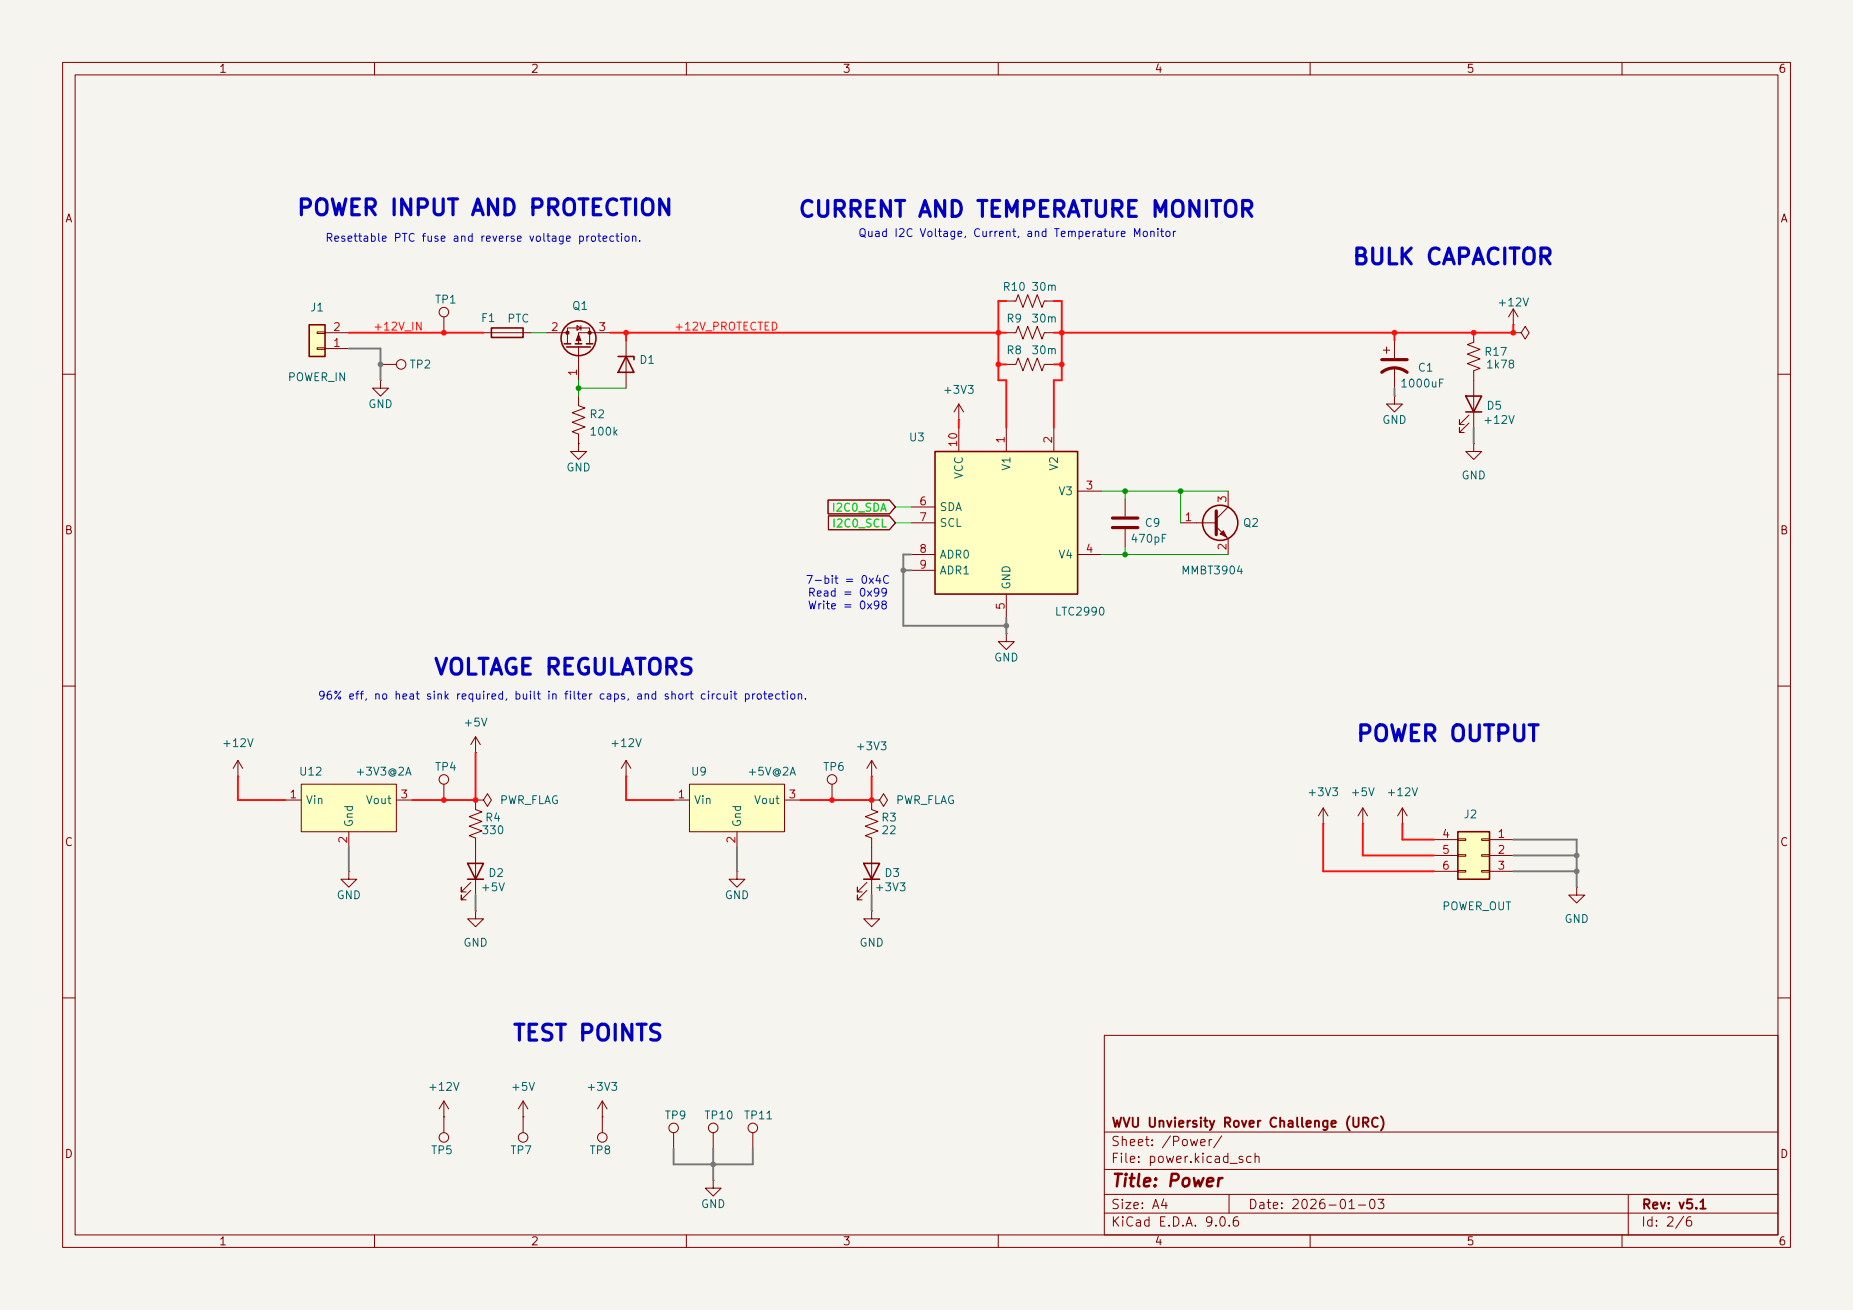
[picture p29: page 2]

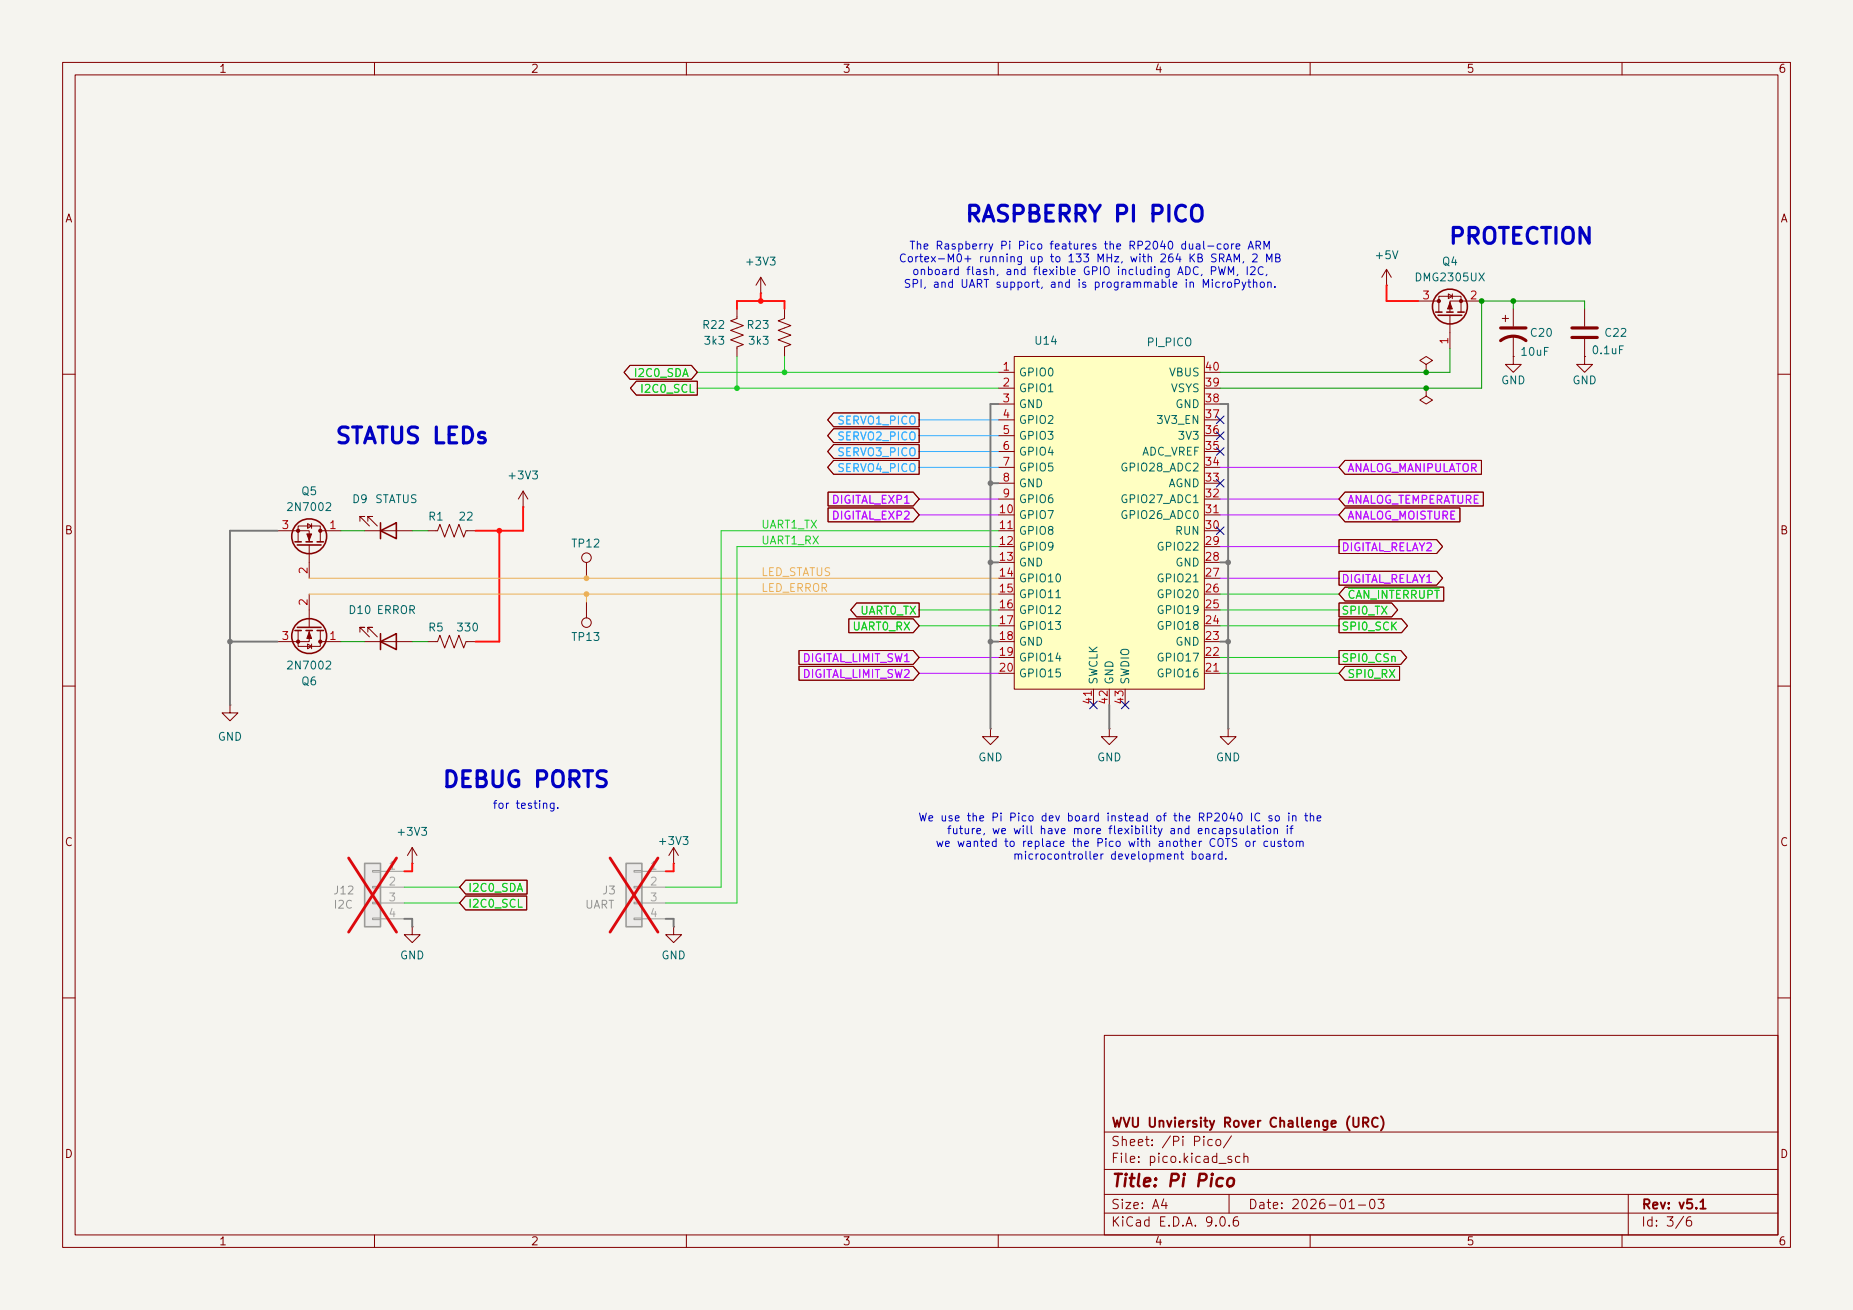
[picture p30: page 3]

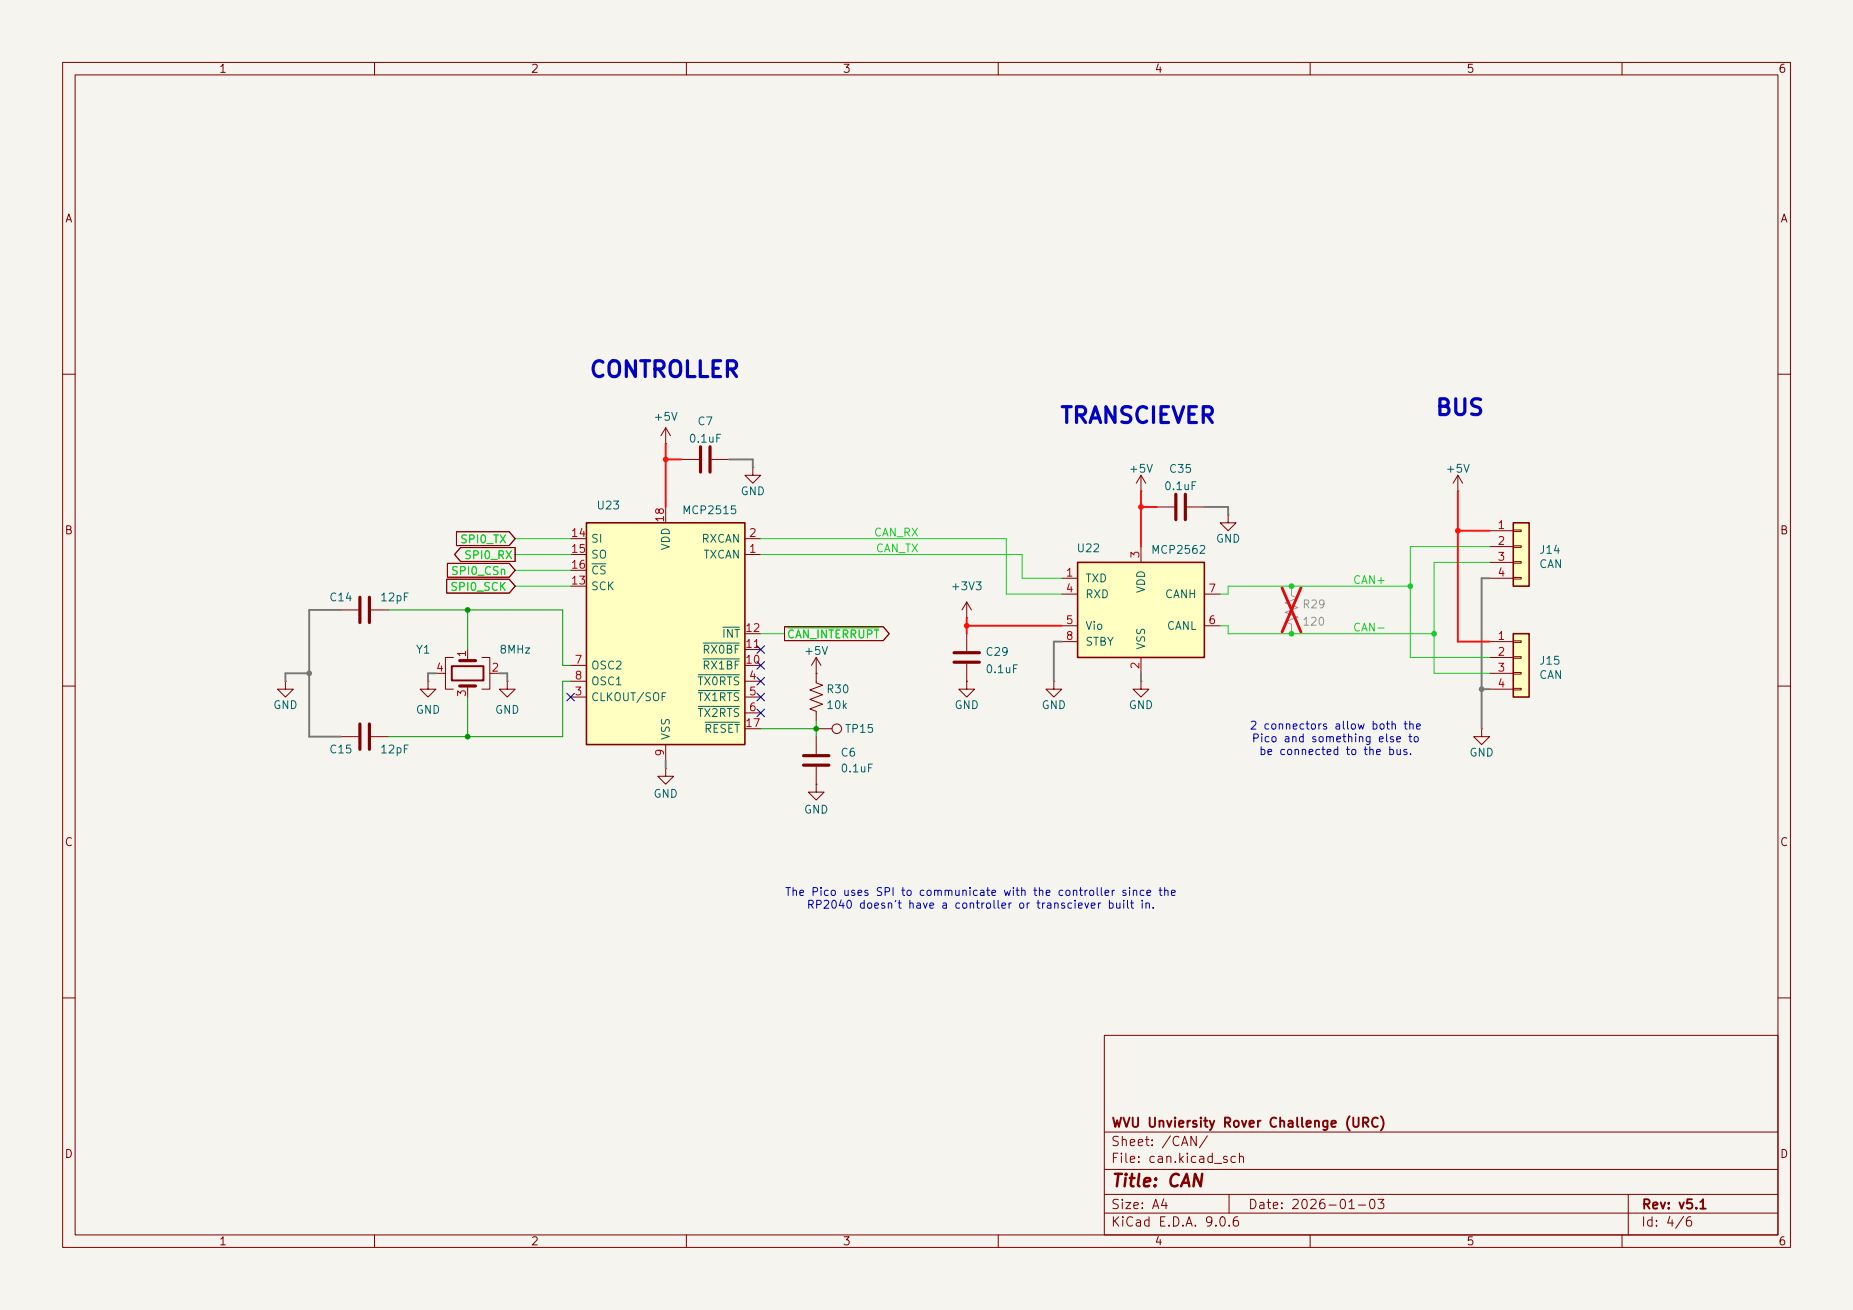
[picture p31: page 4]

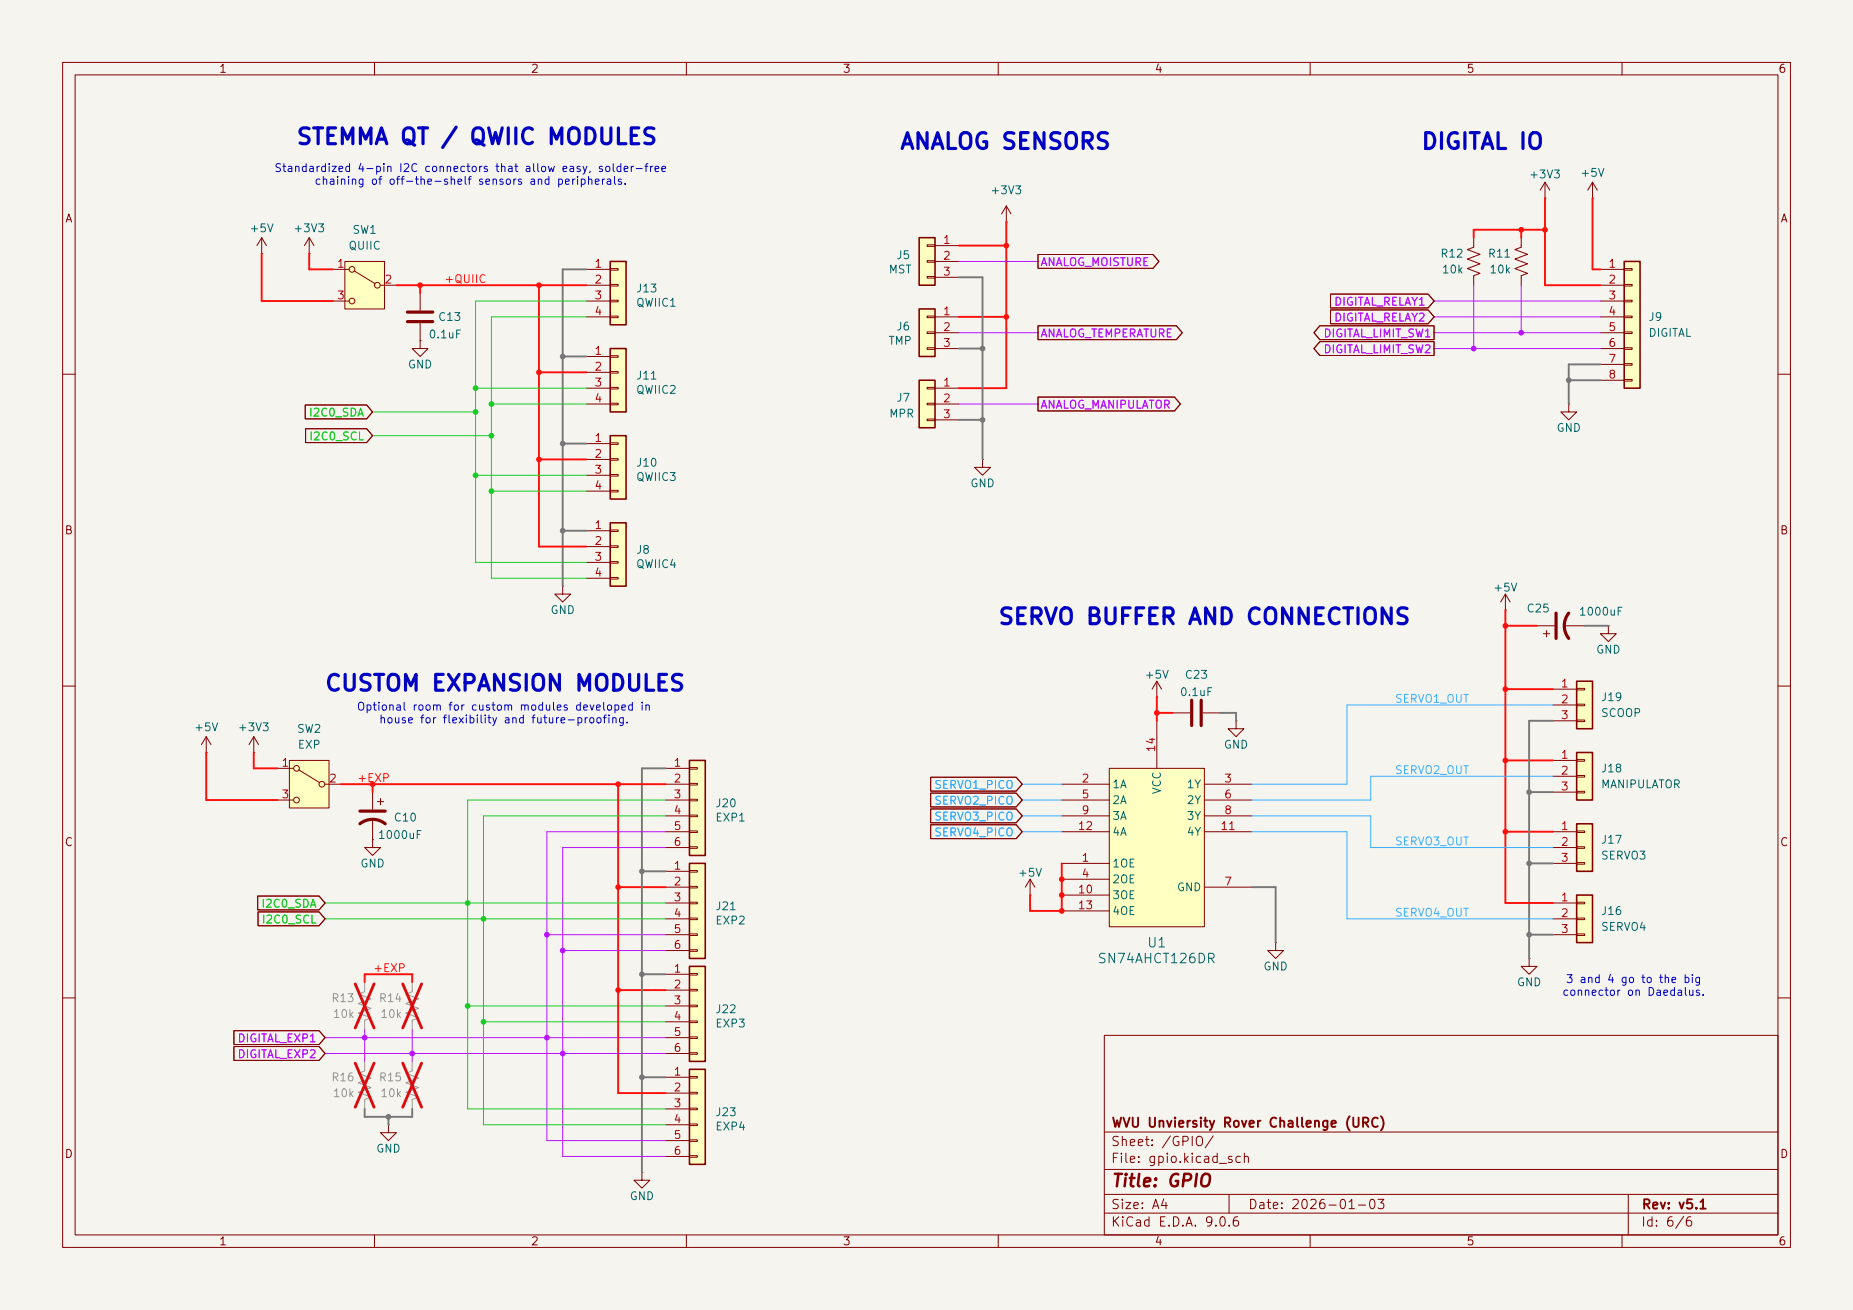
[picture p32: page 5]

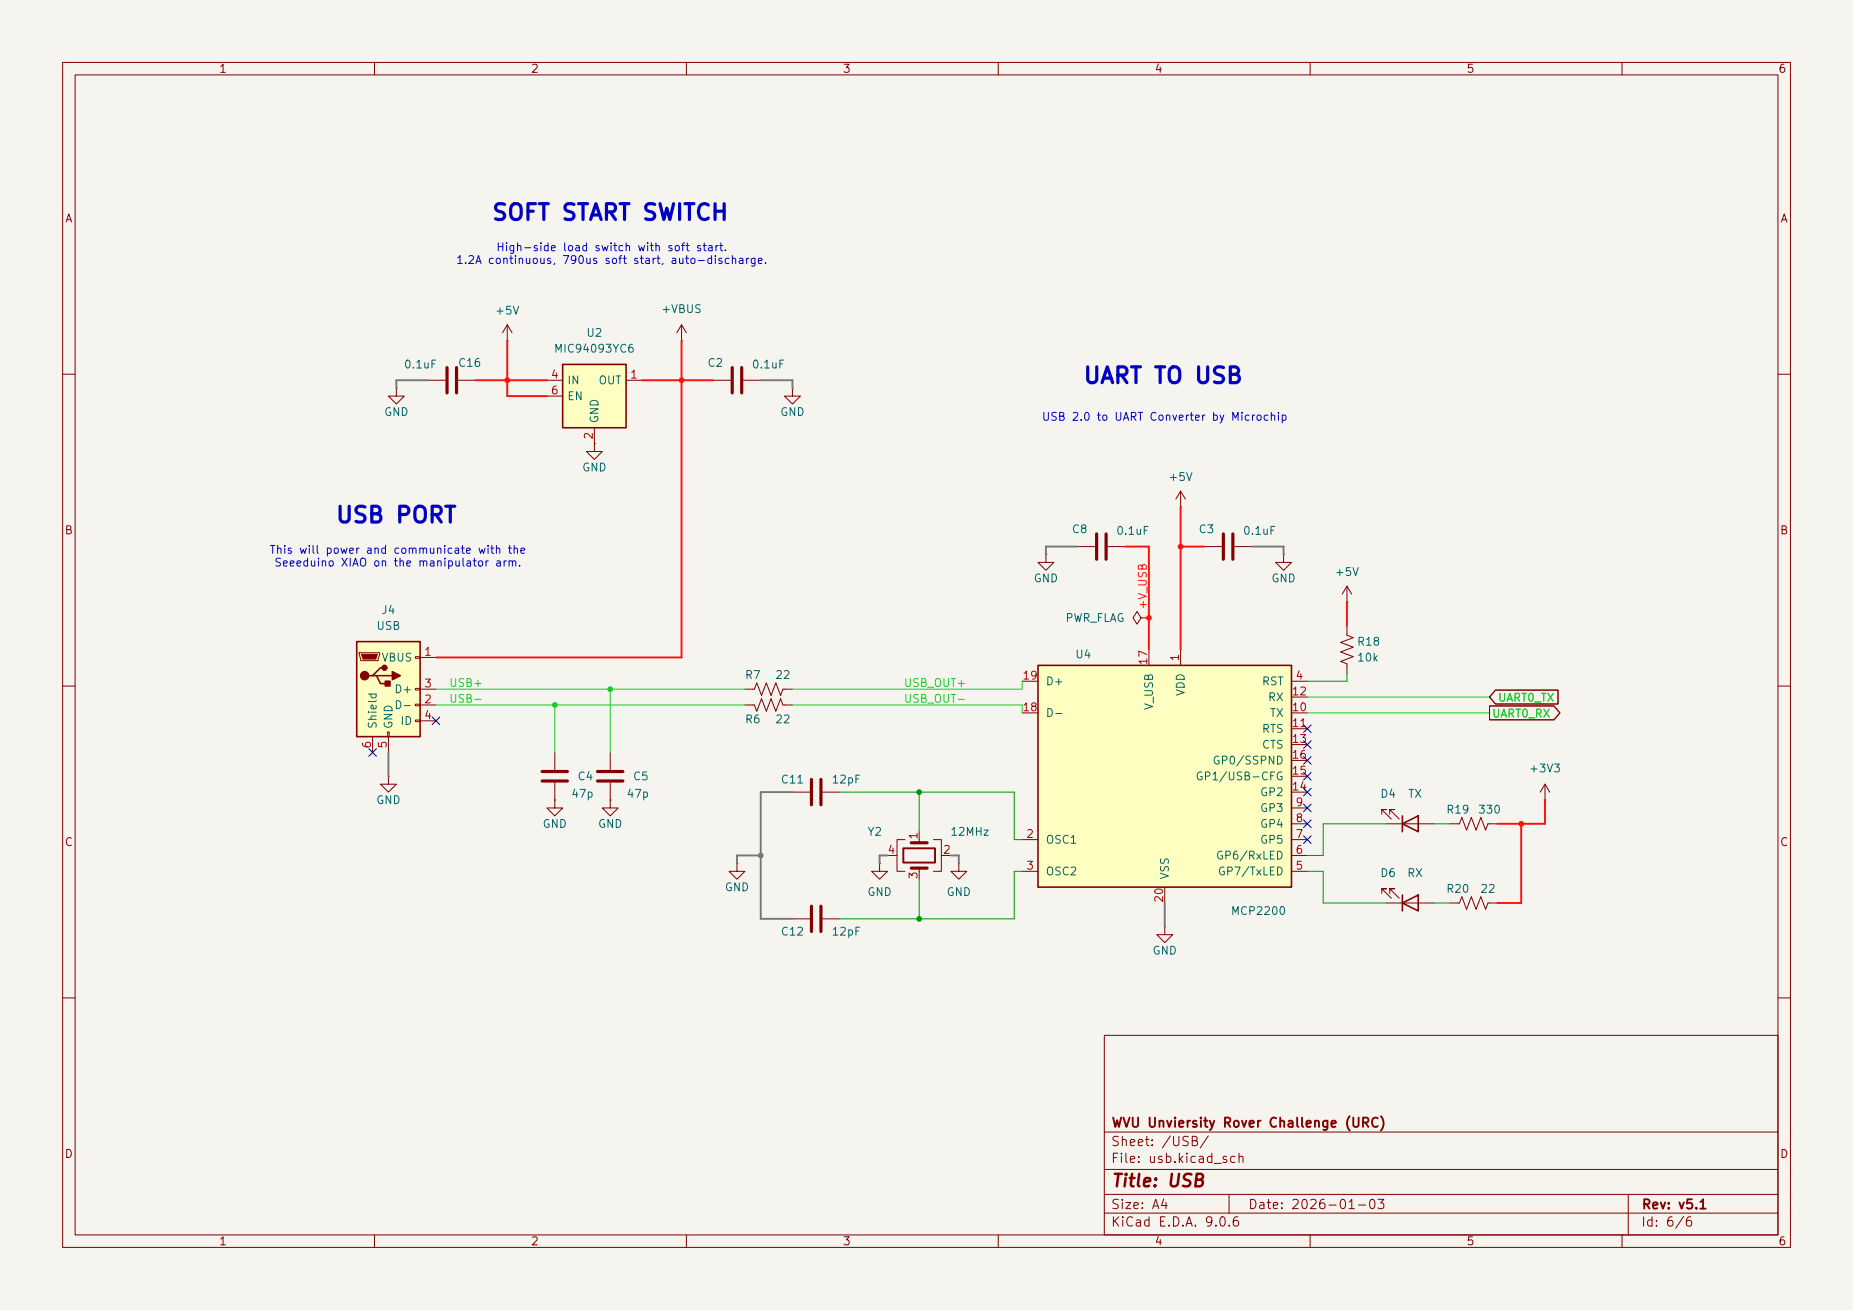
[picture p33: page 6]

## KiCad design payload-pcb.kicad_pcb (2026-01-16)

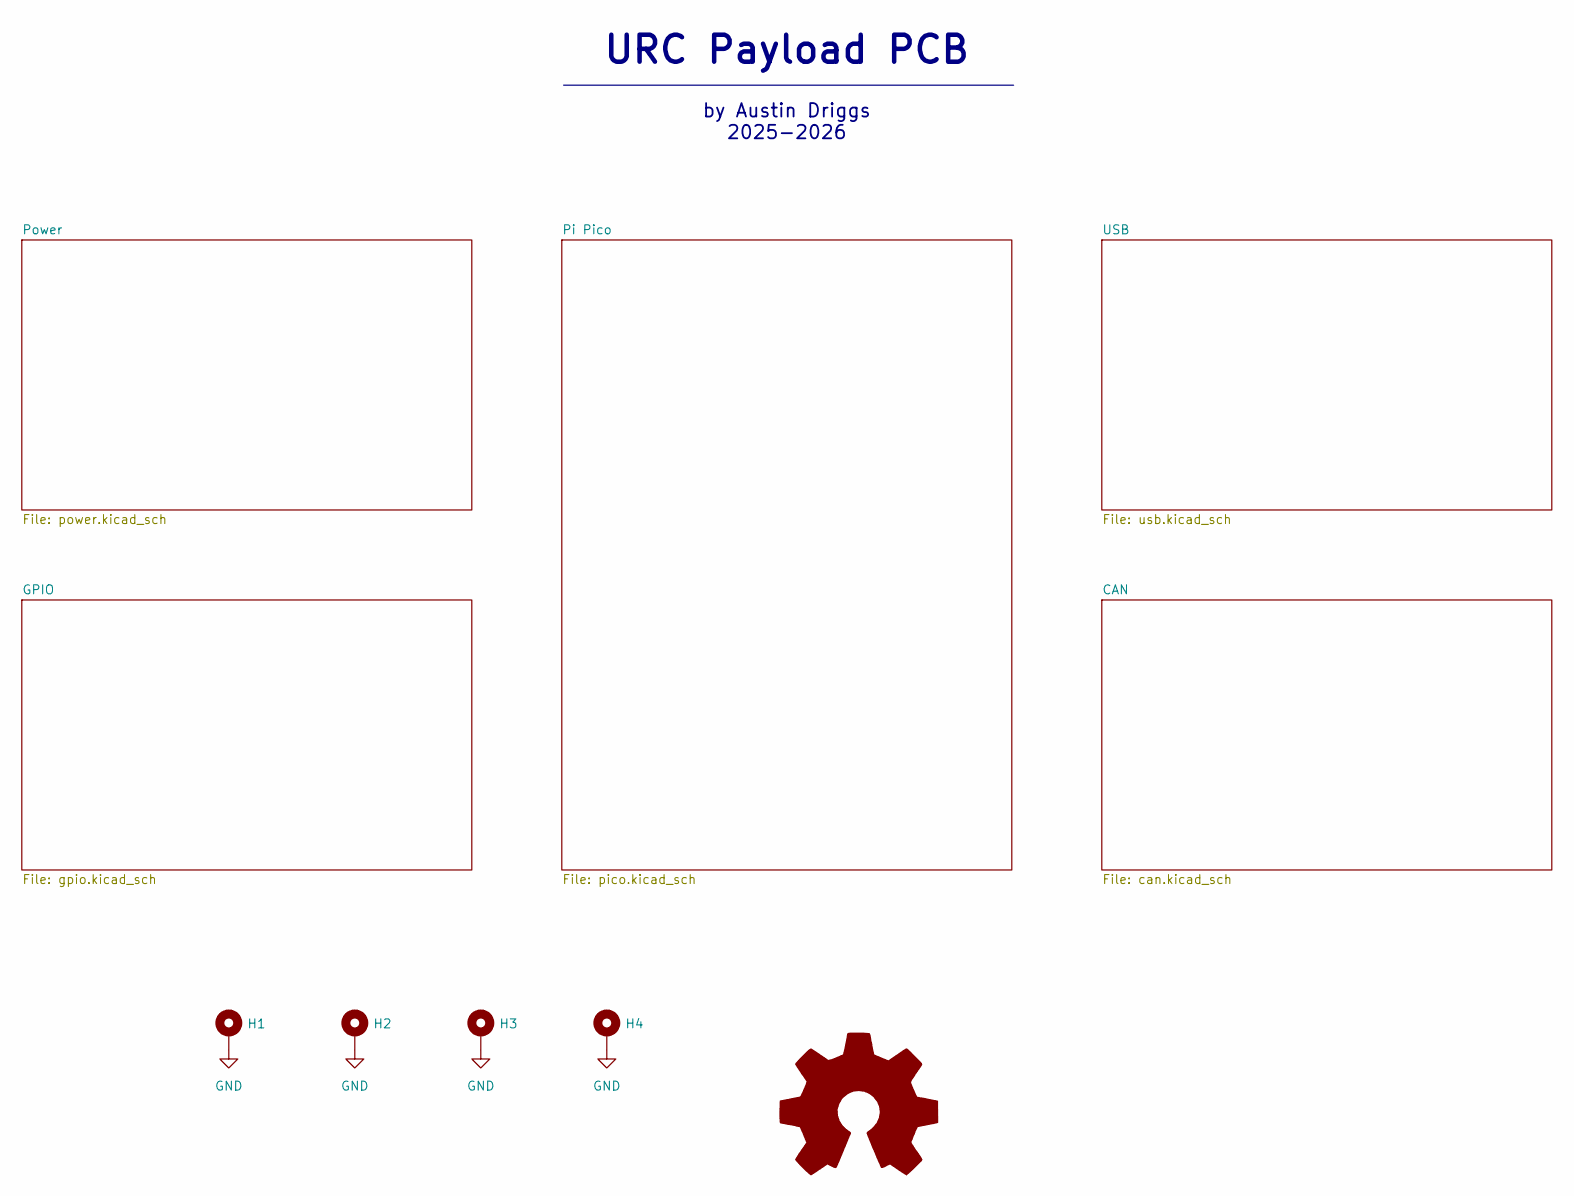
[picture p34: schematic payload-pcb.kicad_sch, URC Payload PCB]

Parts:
H1, H2, H3, H4: MountingHole; MountingHole_3.2mm_M3_DIN965_Pad

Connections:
GND: H1.1, H2.1, H3.1, H4.1; also elsewhere on the board

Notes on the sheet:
URC Payload PCB
by Austin Driggs 2025-2026

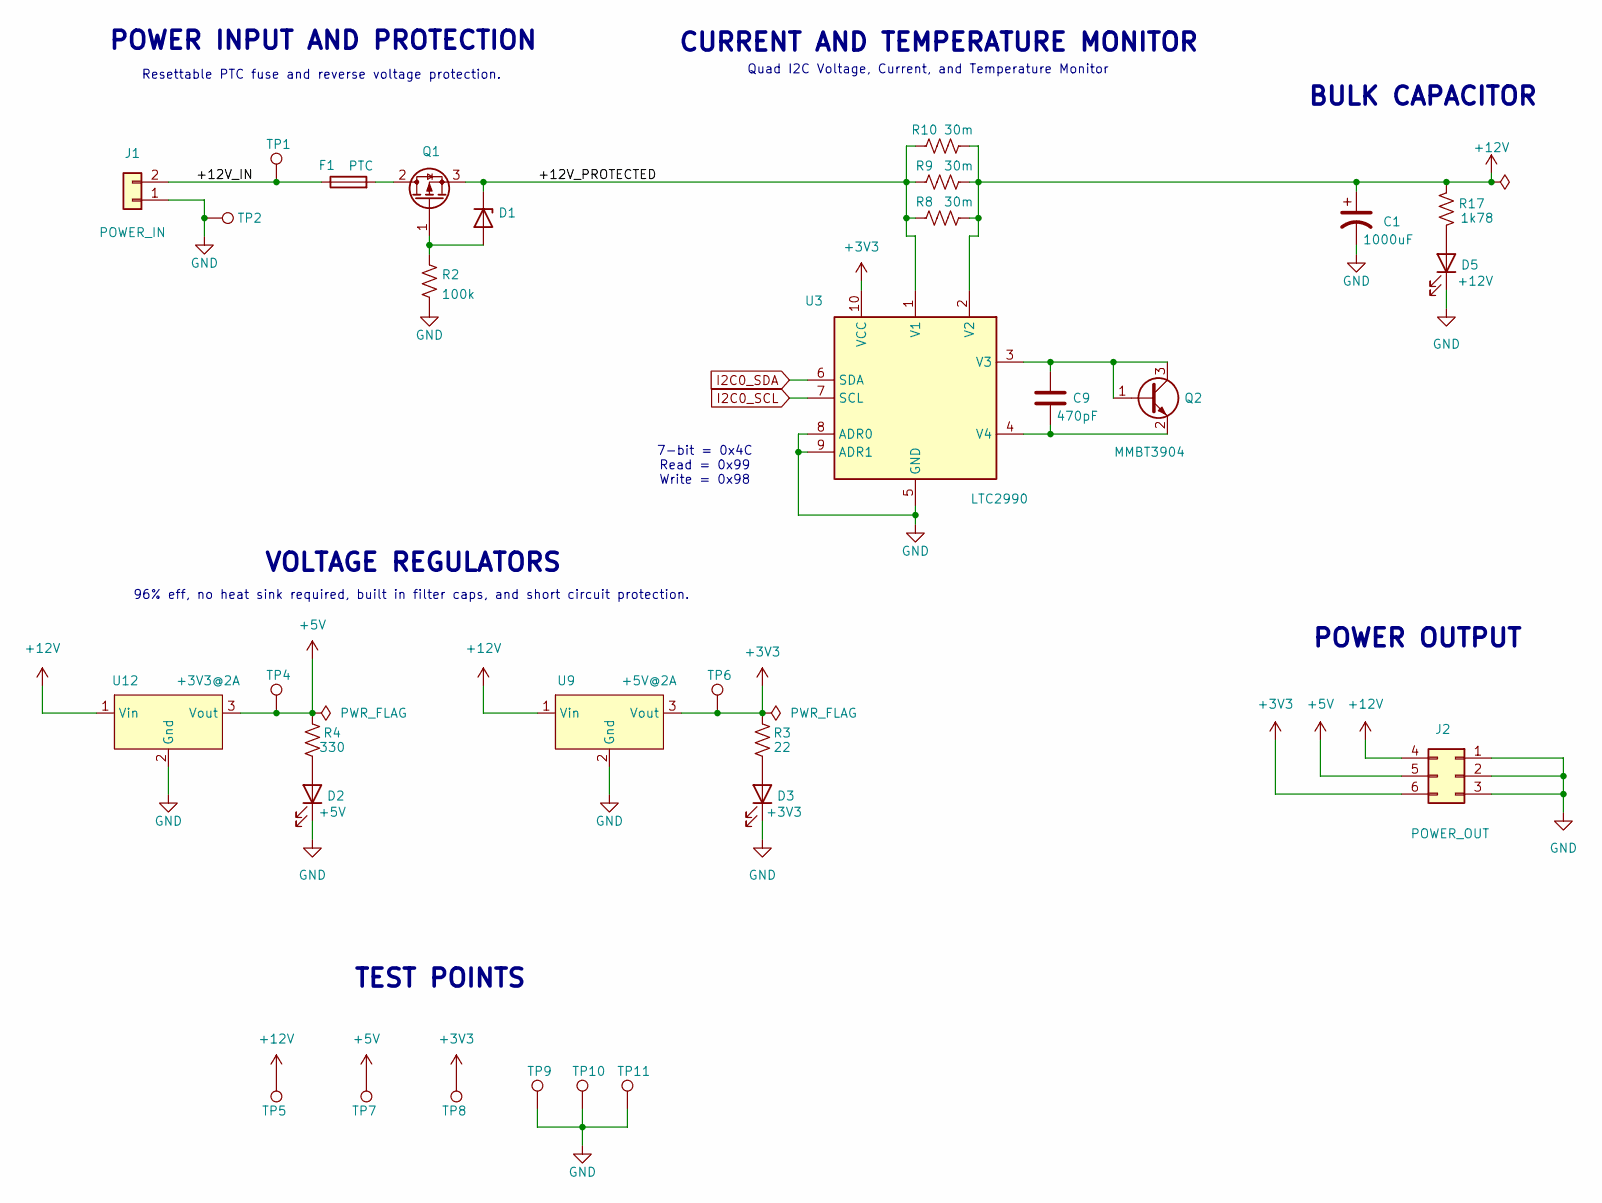
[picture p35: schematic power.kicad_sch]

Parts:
C1: 1000uF; CP_Radial_D10.0mm_P5.00mm; Manufacturer Part Number UVR1E102MPD
C9: 470pF; C_0603_1608Metric_Pad1.08x0.95mm_HandSolder; Manufacturer Part Number C0603C471K5RACTU
D1: BZT52C10-TP; D_SOD-123; Manufacturer Part Number BZT52C10-TP
D2: +5V; LED_0805_2012Metric_Pad1.15x1.40mm_HandSolder; Manufacturer Part Number 150080GS75000
D3: +3V3; LED_0805_2012Metric_Pad1.15x1.40mm_HandSolder; Manufacturer Part Number 150080GS75000
D5: +12V; LED_0805_2012Metric_Pad1.15x1.40mm_HandSolder; Manufacturer Part Number 150080GS75000
F1: PTC; Fuse_1210_3225Metric; Manufacturer Part Number 1210L150/16WR
J1: POWER_IN; Molex_Micro-Fit_3.0_43045-0200_2x01_P3.00mm_Horizontal; Manufacturer Part Number 0430450200
J2: POWER_OUT; Molex_Micro-Fit_3.0_43045-0600_2x03_P3.00mm_Horizontal; Manufacturer Part Number 0430450602
Q1: SUD50P10-43L-GE3; TO-252-2; Manufacturer Part Number SUD50P10-43L-GE3
Q2: MMBT3904; SOT-23; Manufacturer Part Number MMBT3904LT1G
R2: 100k; R_0603_1608Metric_Pad0.98x0.95mm_HandSolder; Manufacturer Part Number RMCF0603FT100K
R3: 22; R_0603_1608Metric_Pad0.98x0.95mm_HandSolder; Manufacturer Part Number RNCP0603FTD22R1
R4: 330; R_0603_1608Metric_Pad0.98x0.95mm_HandSolder; Manufacturer Part Number RNCP0603FTD332R
R8, R9, R10: 30m; R_1206_3216Metric_Pad1.30x1.75mm_HandSolder; Manufacturer Part Number CSR1206FT30L0
R17: 1k78; R_0603_1608Metric_Pad0.98x0.95mm_HandSolder; Manufacturer Part Number RNCP0603FTD1K78
TP1: +12V_IN; TestPoint_Pad_D2.0mm
TP2, TP9, TP10, TP11: GND; TestPoint_Pad_D2.0mm
TP4, TP7: +5V; TestPoint_Pad_D2.0mm
TP5: +12V; TestPoint_Pad_D2.0mm
TP6, TP8: +3V3; TestPoint_Pad_D2.0mm
U3: LTC2990; MSOP-10_3x3mm_P0.5mm; Manufacturer Part Number LTC2990IMS#TRPBF
U9: +5V@2A; TSR_2-24xx; Manufacturer Part Number TSR 2-2450
U12: +3V3@2A; TSR_2-24xx; Manufacturer Part Number TSR 2-2433

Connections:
+3V3: J2.6, R3.2, TP6.1, TP8.1, U3.10 (VCC), U9.3 (Vout); also elsewhere on the board
+5V: J2.5, R4.2, TP4.1, TP7.1, U12.3 (Vout); also elsewhere on the board
+12V: C1.1, J2.4, R8.2, R9.2, R10.2, R17.2, TP5.1, U3.2 (V2), U9.1 (Vin), U12.1 (Vin)
/Power/+12V_IN: F1.1, J1.2, TP1.1
/Power/+12V_PROTECTED: D1.1 (K), Q1.3 (S), R8.1, R9.1, R10.1, U3.1 (V1)
GND: C1.2, D2.1 (K), D3.1 (K), D5.1 (K), J1.1, J2.1, J2.2, J2.3, R2.2, TP2.1, TP9.1, TP10.1, TP11.1, U3.5 (GND), U3.8 (ADR0), U3.9 (ADR1), U9.2 (Gnd), U12.2 (Gnd); also elsewhere on the board
I2C0_SCL: U3.7 (SCL); also elsewhere on the board
I2C0_SDA: U3.6 (SDA); also elsewhere on the board
unnamed: D1.2 (A), Q1.1 (G), R2.1
unnamed: D2.2 (A), R4.1
unnamed: D3.2 (A), R3.1
unnamed: D5.2 (A), R17.1
unnamed: F1.2, Q1.2 (D)
unnamed: C9.2, Q2.1 (B), Q2.3 (C), U3.3 (V3)
unnamed: C9.1, Q2.2 (E), U3.4 (V4)

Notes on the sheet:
96% eff, no heat sink required, built in filter caps, and short circuit protection.
CURRENT AND TEMPERATURE MONITOR
BULK CAPACITOR
VOLTAGE REGULATORS
Resettable PTC fuse and reverse voltage protection.
TEST POINTS
POWER OUTPUT
7-bit = 0x4C Read = 0x99 Write = 0x98
POWER INPUT AND PROTECTION
Quad I2C Voltage, Current, and Temperature Monitor

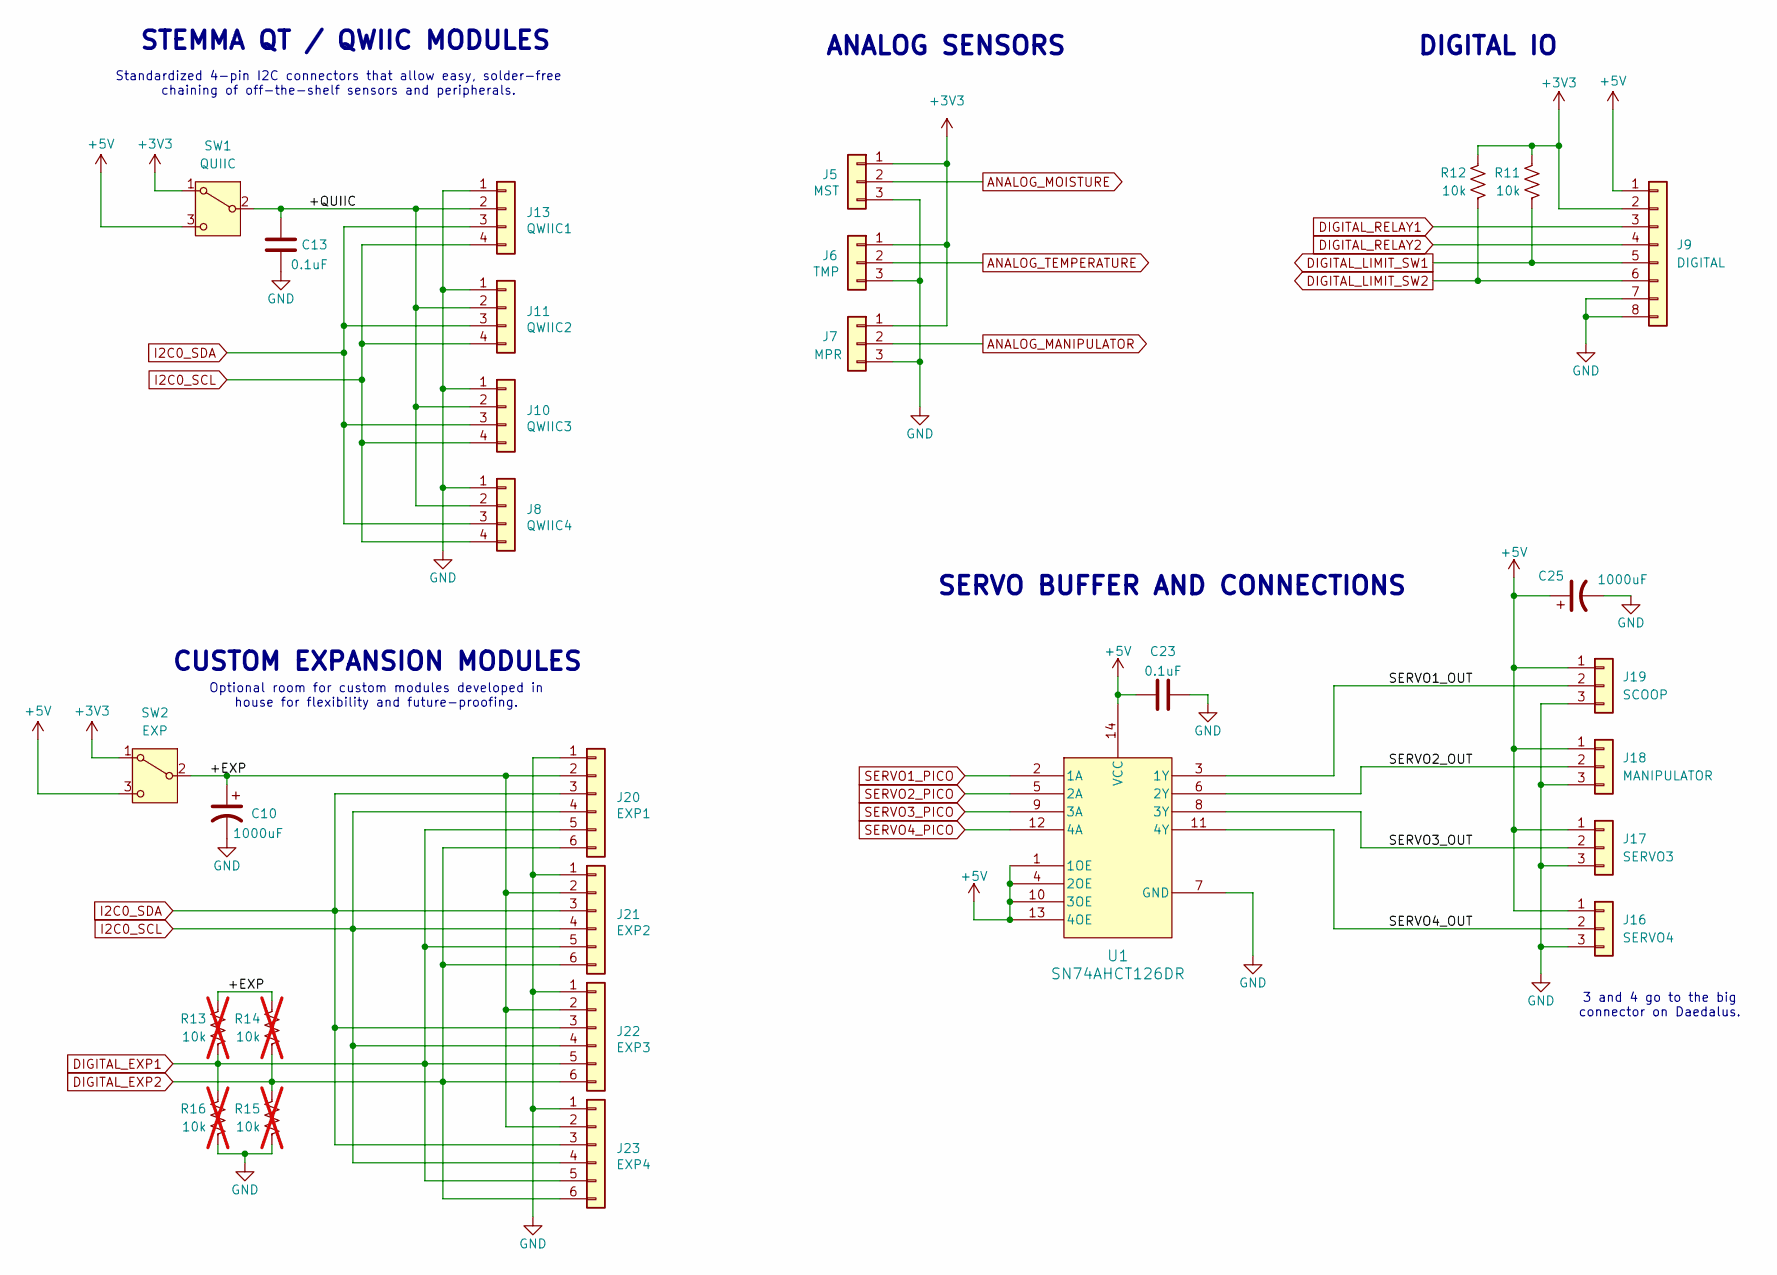
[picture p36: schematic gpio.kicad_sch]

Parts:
C10, C25: 1000uF; CP_Radial_D10.0mm_P5.00mm; Manufacturer Part Number UVR1E102MPD
C13, C23: 0.1uF; C_1206_3216Metric_Pad1.33x1.80mm_HandSolder; Manufacturer Part Number C1206C104J5RACTU
J5: MST; Molex_PicoBlade_53047-0310_1x03_P1.25mm_Vertical; Manufacturer Part Number 0530470310
J6: TMP; Molex_PicoBlade_53047-0310_1x03_P1.25mm_Vertical; Manufacturer Part Number 0530470310
J7: MPR; Molex_PicoBlade_53047-0310_1x03_P1.25mm_Vertical; Manufacturer Part Number 0530470310
J8: QWIIC4; JST_GH_BM04B-GHS-TBT_1x04-1MP_P1.25mm_Vertical; Manufacturer Part Number SM04B-GHS-TB
J9: DIGITAL; Molex_PicoBlade_53047-0810_1x08_P1.25mm_Vertical; Manufacturer Part Number 0530470810
J10: QWIIC3; JST_GH_BM04B-GHS-TBT_1x04-1MP_P1.25mm_Vertical; Manufacturer Part Number SM04B-GHS-TB
J11: QWIIC2; JST_GH_BM04B-GHS-TBT_1x04-1MP_P1.25mm_Vertical; Manufacturer Part Number SM04B-GHS-TB
J13: QWIIC1; JST_GH_BM04B-GHS-TBT_1x04-1MP_P1.25mm_Vertical; Manufacturer Part Number SM04B-GHS-TB
J16: SERVO4; Molex_PicoBlade_53047-0310_1x03_P1.25mm_Vertical; Manufacturer Part Number 0530470310
J17: SERVO3; Molex_PicoBlade_53047-0310_1x03_P1.25mm_Vertical; Manufacturer Part Number 0530470310
J18: MANIPULATOR; Molex_PicoBlade_53047-0310_1x03_P1.25mm_Vertical; Manufacturer Part Number 0530470310
J19: SCOOP; Molex_PicoBlade_53047-0310_1x03_P1.25mm_Vertical; Manufacturer Part Number 0530470310
J20: EXP1; PinSocket_1x06_P2.54mm_Vertical; Manufacturer Part Number SSW-106-01-F-S
J21: EXP2; PinSocket_1x06_P2.54mm_Vertical; Manufacturer Part Number SSW-106-01-F-S
J22: EXP3; PinSocket_1x06_P2.54mm_Vertical; Manufacturer Part Number SSW-106-01-F-S
J23: EXP4; PinSocket_1x06_P2.54mm_Vertical; Manufacturer Part Number SSW-106-01-F-S
R11, R12: 10k; R_0603_1608Metric_Pad0.98x0.95mm_HandSolder; Manufacturer Part Number RNCP0603FTD10K0
R13, R14, R15, R16: 10k; R_0603_1608Metric_Pad0.98x0.95mm_HandSolder; Manufacturer Part Number RNCP0603FTD10K0; not fitted
SW1: QUIIC; SW_E-Switch_EG1271_SPDT; Manufacturer Part Number EG1271A
SW2: EXP; SW_E-Switch_EG1271_SPDT; Manufacturer Part Number EG1271A
U1: SN74AHCT126DR; SOIC-14_3.9x8.7mm_P1.27mm; Manufacturer Part Number SN74AHCT126DR

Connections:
+3V3: J5.1, J6.1, J7.1, J9.2, R11.2, R12.2, SW1.1 (A), SW2.1 (A); also elsewhere on the board
+5V: C23.1, C25.1, J9.1, J16.1, J17.1, J18.1, J19.1, SW1.3 (C), SW2.3 (C), U1.1 (1OE), U1.4 (2OE), U1.10 (3OE), U1.13 (4OE), U1.14 (VCC); also elsewhere on the board
/GPIO/+EXP: C10.1, J20.2, J21.2, J22.2, J23.2, R13.2, R14.2, SW2.2 (B)
/GPIO/+QUIIC: C13.2, J8.2, J10.2, J11.2, J13.2, SW1.2 (B)
/GPIO/SERVO1_OUT: J19.2, U1.3 (1Y)
/GPIO/SERVO2_OUT: J18.2, U1.6 (2Y)
/GPIO/SERVO3_OUT: J17.2, U1.8 (3Y)
/GPIO/SERVO4_OUT: J16.2, U1.11 (4Y)
ANALOG_MANIPULATOR: J7.2; also elsewhere on the board
ANALOG_MOISTURE: J5.2; also elsewhere on the board
ANALOG_TEMPERATURE: J6.2; also elsewhere on the board
DIGITAL_EXP1: J20.5, J21.5, J22.5, J23.5, R13.1, R16.2; also elsewhere on the board
DIGITAL_EXP2: J20.6, J21.6, J22.6, J23.6, R14.1, R15.2; also elsewhere on the board
DIGITAL_LIMIT_SW1: J9.5, R11.1; also elsewhere on the board
DIGITAL_LIMIT_SW2: J9.6, R12.1; also elsewhere on the board
DIGITAL_RELAY1: J9.3; also elsewhere on the board
DIGITAL_RELAY2: J9.4; also elsewhere on the board
GND: C10.2, C13.1, C23.2, C25.2, J5.3, J6.3, J7.3, J8.1, J9.7, J9.8, J10.1, J11.1, J13.1, J16.3, J17.3, J18.3, J19.3, J20.1, J21.1, J22.1, J23.1, R15.1, R16.1, U1.7 (GND); also elsewhere on the board
I2C0_SCL: J8.4, J10.4, J11.4, J13.4, J20.4, J21.4, J22.4, J23.4; also elsewhere on the board
I2C0_SDA: J8.3, J10.3, J11.3, J13.3, J20.3, J21.3, J22.3, J23.3; also elsewhere on the board
SERVO1_PICO: U1.2 (1A); also elsewhere on the board
SERVO2_PICO: U1.5 (2A); also elsewhere on the board
SERVO3_PICO: U1.9 (3A); also elsewhere on the board
SERVO4_PICO: U1.12 (4A); also elsewhere on the board

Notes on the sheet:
STEMMA QT / QWIIC MODULES
3 and 4 go to the big connector on Daedalus.
CUSTOM EXPANSION MODULES
Standardized 4-pin I2C connectors that allow easy, solder-free chaining of off-the-shelf sensors and peripherals.
ANALOG SENSORS
SERVO BUFFER AND CONNECTIONS
Optional room for custom modules developed in house for flexibility and future-proofing.
DIGITAL IO

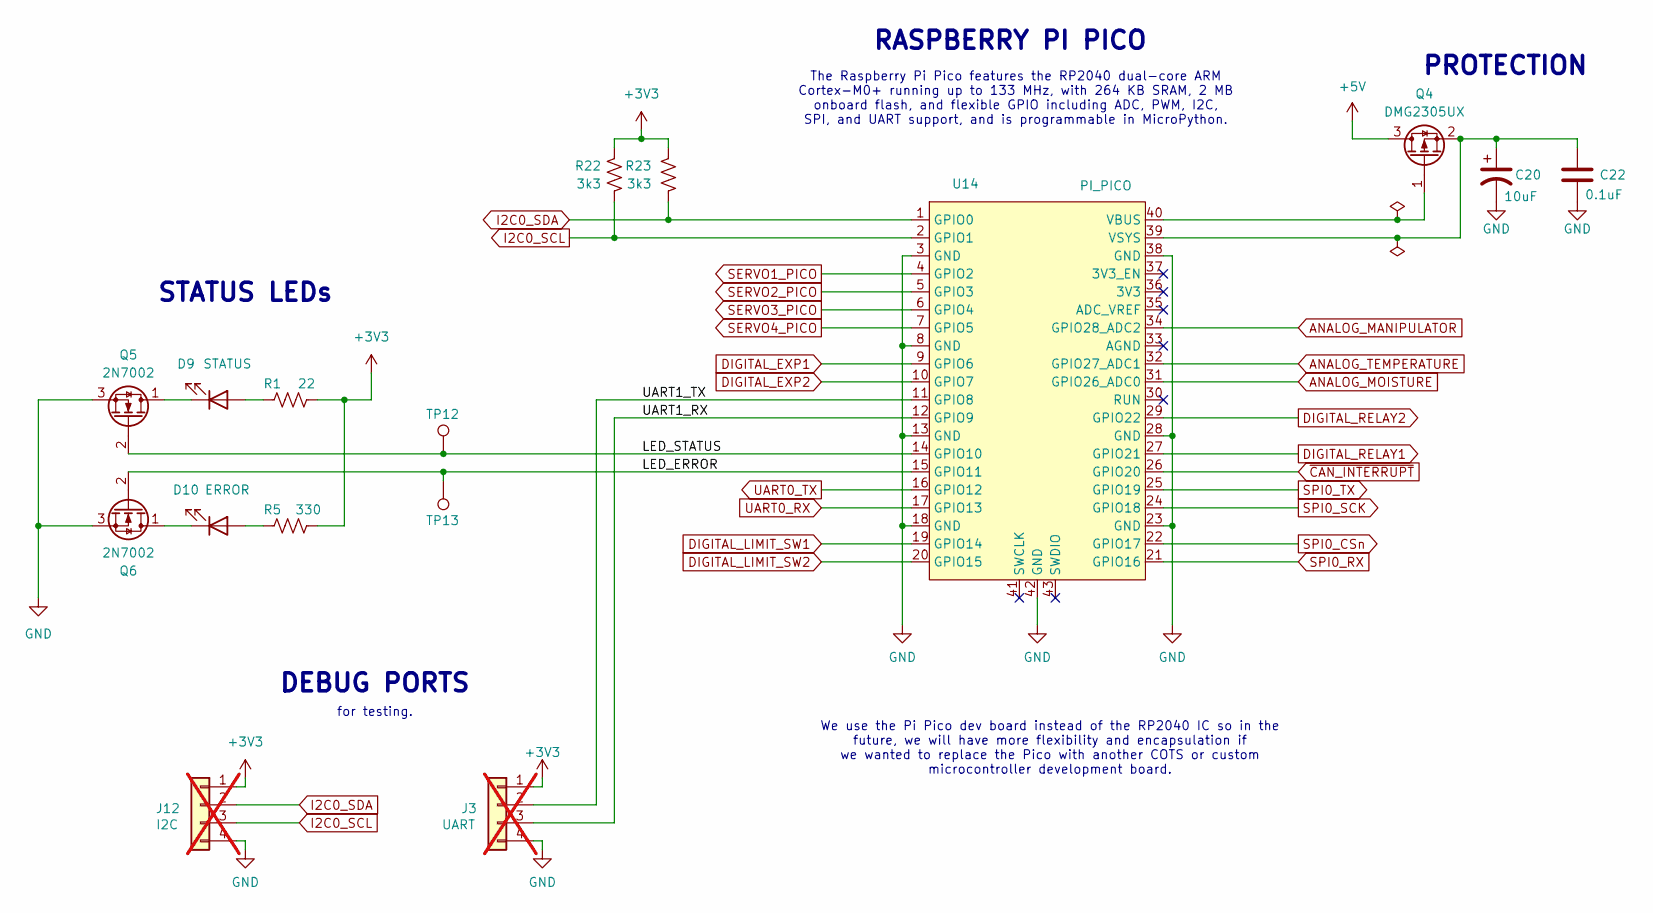
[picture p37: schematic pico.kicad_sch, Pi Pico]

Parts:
C20: 10uF; CP_Radial_D8.0mm_P2.50mm; Manufacturer Part Number UVR2C100MPD1TD
C22: 0.1uF; C_1206_3216Metric_Pad1.33x1.80mm_HandSolder; Manufacturer Part Number C1206C104J5RACTU
D9: STATUS; LED_0805_2012Metric_Pad1.15x1.40mm_HandSolder; Manufacturer Part Number 150080BS75000
D10: ERROR; LED_0805_2012Metric_Pad1.15x1.40mm_HandSolder; Manufacturer Part Number 150080RS75000
J3: UART; Molex_PicoBlade_53047-0410_1x04_P1.25mm_Vertical; Manufacturer Part Number 0530470410; not fitted
J12: I2C; Molex_PicoBlade_53047-0410_1x04_P1.25mm_Vertical; Manufacturer Part Number 0530470410; not fitted
Q4: DMG2305UX; SOT-23; Manufacturer Part Number DMG2305UX-7
Q5, Q6: 2N7002; TSOT-23; Manufacturer Part Number 2N7002
R1: 22; R_0603_1608Metric_Pad0.98x0.95mm_HandSolder; Manufacturer Part Number RNCP0603FTD22R1
R5: 330; R_0603_1608Metric_Pad0.98x0.95mm_HandSolder; Manufacturer Part Number RNCP0603FTD332R
R22, R23: 3k3; R_0603_1608Metric_Pad0.98x0.95mm_HandSolder; Manufacturer Part Number RNCP0603FTD3K30
TP12: LED1; TestPoint_Pad_D1.0mm
TP13: LED2; TestPoint_Pad_D1.0mm
U14: PI_PICO; RPi_Pico_SMD_TH; Manufacturer Part Number SC0915

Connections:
+3V3: J3.1, J12.1, R1.2, R5.1, R22.2, R23.2; also elsewhere on the board
+5V: Q4.3 (D); also elsewhere on the board
/Pi Pico/LED_ERROR: Q6.2 (G), TP13.1, U14.15 (GPIO11)
/Pi Pico/LED_STATUS: Q5.2 (G), TP12.1, U14.14 (GPIO10)
/Pi Pico/UART1_RX: J3.3, U14.12 (GPIO9)
/Pi Pico/UART1_TX: J3.2, U14.11 (GPIO8)
ANALOG_MANIPULATOR: U14.34 (GPIO28_ADC2); also elsewhere on the board
ANALOG_MOISTURE: U14.31 (GPIO26_ADC0); also elsewhere on the board
ANALOG_TEMPERATURE: U14.32 (GPIO27_ADC1); also elsewhere on the board
DIGITAL_EXP1: U14.9 (GPIO6); also elsewhere on the board
DIGITAL_EXP2: U14.10 (GPIO7); also elsewhere on the board
DIGITAL_LIMIT_SW1: U14.19 (GPIO14); also elsewhere on the board
DIGITAL_LIMIT_SW2: U14.20 (GPIO15); also elsewhere on the board
DIGITAL_RELAY1: U14.27 (GPIO21); also elsewhere on the board
DIGITAL_RELAY2: U14.29 (GPIO22); also elsewhere on the board
GND: C20.2, C22.1, J3.4, J12.4, Q5.3 (S), Q6.3 (S), U14.3 (GND), U14.8 (GND), U14.13 (GND), U14.18 (GND), U14.23 (GND), U14.28 (GND), U14.38 (GND), U14.42 (GND); also elsewhere on the board
I2C0_SCL: J12.3, R22.1, U14.2 (GPIO1); also elsewhere on the board
I2C0_SDA: J12.2, R23.1, U14.1 (GPIO0); also elsewhere on the board
unnamed: D9.2 (A), R1.1
unnamed: D9.1 (K), Q5.1 (D)
unnamed: D10.2 (A), R5.2
unnamed: D10.1 (K), Q6.1 (D)
unnamed: Q4.1 (G), U14.40 (VBUS)
unnamed: C20.1, C22.2, Q4.2 (S), U14.39 (VSYS)
SERVO1_PICO: U14.4 (GPIO2); also elsewhere on the board
SERVO2_PICO: U14.5 (GPIO3); also elsewhere on the board
SERVO3_PICO: U14.6 (GPIO4); also elsewhere on the board
SERVO4_PICO: U14.7 (GPIO5); also elsewhere on the board
SPI0_CSn: U14.22 (GPIO17); also elsewhere on the board
SPI0_RX: U14.21 (GPIO16); also elsewhere on the board
SPI0_SCK: U14.24 (GPIO18); also elsewhere on the board
SPI0_TX: U14.25 (GPIO19); also elsewhere on the board
UART0_RX: U14.17 (GPIO13); also elsewhere on the board
UART0_TX: U14.16 (GPIO12); also elsewhere on the board
~CAN_INTERRUPT: U14.26 (GPIO20); also elsewhere on the board

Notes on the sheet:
RASPBERRY PI PICO
PROTECTION
DEBUG PORTS
for testing.
We use the Pi Pico dev board instead of the RP2040 IC so in the future, we will have more flexibility and encapsulation if we wanted to replace the Pico with another COTS or custom microcontroller development board.
The Raspberry Pi Pico features the RP2040 dual-core ARM Cortex-M0+ running up to 133 MHz, with 264 KB SRAM, 2 MB onboard flash, and flexible GPIO including ADC, PWM, I2C, SPI, and UART support, and is programmable in MicroPython.
STATUS LEDs

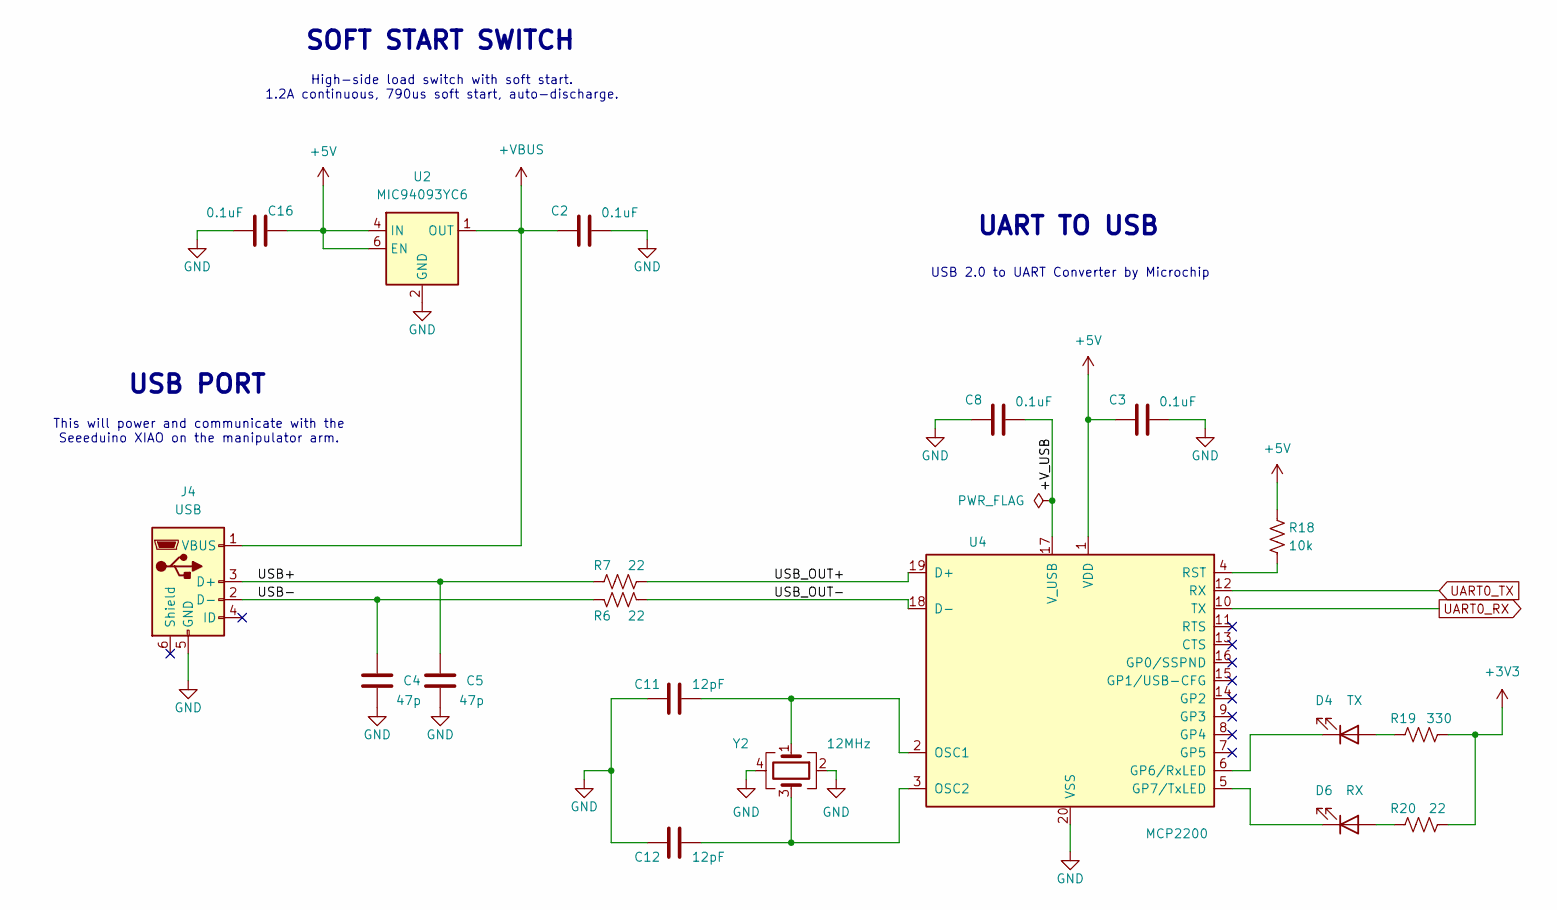
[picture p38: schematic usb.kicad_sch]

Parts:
C2, C3, C8, C16: 0.1uF; C_0805_2012Metric_Pad1.18x1.45mm_HandSolder; Manufacturer Part Number C1206C104J5RACTU
C4, C5: 47p; C_0603_1608Metric_Pad1.08x0.95mm_HandSolder; Manufacturer Part Number C0603C470K5RACTU
C11, C12: 12pF; C_0603_1608Metric_Pad1.08x0.95mm_HandSolder; Manufacturer Part Number C0603C120K5RACTU
D4: TX; LED_0805_2012Metric_Pad1.15x1.40mm_HandSolder; Manufacturer Part Number 150080GS75000
D6: RX; LED_0805_2012Metric_Pad1.15x1.40mm_HandSolder; Manufacturer Part Number 150080GS75000
J4: USB; USB_Micro-B_Wuerth_629105150521; Manufacturer Part Number 629105150521
R6, R7, R20: 22; R_0603_1608Metric_Pad0.98x0.95mm_HandSolder; Manufacturer Part Number RNCP0603FTD22R1
R18: 10k; R_0603_1608Metric_Pad0.98x0.95mm_HandSolder; Manufacturer Part Number RNCP0603FTD10K0
R19: 330; R_0603_1608Metric_Pad0.98x0.95mm_HandSolder; Manufacturer Part Number RNCP0603FTD332R
U2: MIC94093YC6; SOT-363_SC-70-6; Manufacturer Part Number MIC94093YC6-TR
U4: MCP2200; SSOP-20_5.3x7.2mm_P0.65mm; Manufacturer Part Number 150-MCP2200T-E/SSCT-ND
Y2: 12MHz; Crystal_SMD_2520-4Pin_2.5x2.0mm; Manufacturer Part Number FH1200004

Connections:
+3V3: R19.1, R20.2; also elsewhere on the board
+5V: C3.2, C16.2, R18.2, U2.4 (IN), U2.6 (EN), U4.1 (VDD); also elsewhere on the board
+VBUS: C2.2, J4.1 (VBUS), U2.1 (OUT)
/USB/+V_USB: C8.1, U4.17 (V_USB)
/USB/USB+: C5.2, J4.3 (D+), R7.1
/USB/USB-: C4.2, J4.2 (D-), R6.1
/USB/USB_OUT+: R7.2, U4.19 (D+)
/USB/USB_OUT-: R6.2, U4.18 (D-)
GND: C2.1, C3.1, C4.1, C5.1, C8.2, C11.1, C12.1, C16.1, J4.5 (GND), U2.2 (GND), U2.5 (GND), U4.20 (VSS), Y2.2, Y2.4; also elsewhere on the board
unnamed: D4.2 (A), R19.2
unnamed: D4.1 (K), U4.6 (GP6/RxLED)
unnamed: D6.2 (A), R20.1
unnamed: D6.1 (K), U4.5 (GP7/TxLED)
unnamed: C11.2, U4.2 (OSC1), Y2.1
unnamed: C12.2, U4.3 (OSC2), Y2.3
unnamed: R18.1, U4.4 (RST)
UART0_RX: U4.10 (TX); also elsewhere on the board
UART0_TX: U4.12 (RX); also elsewhere on the board

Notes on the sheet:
USB PORT
This will power and communicate with the Seeeduino XIAO on the manipulator arm.
SOFT START SWITCH
UART TO USB
High-side load switch with soft start. 1.2A continuous, 790us soft start, auto-discharge.
USB 2.0 to UART Converter by Microchip

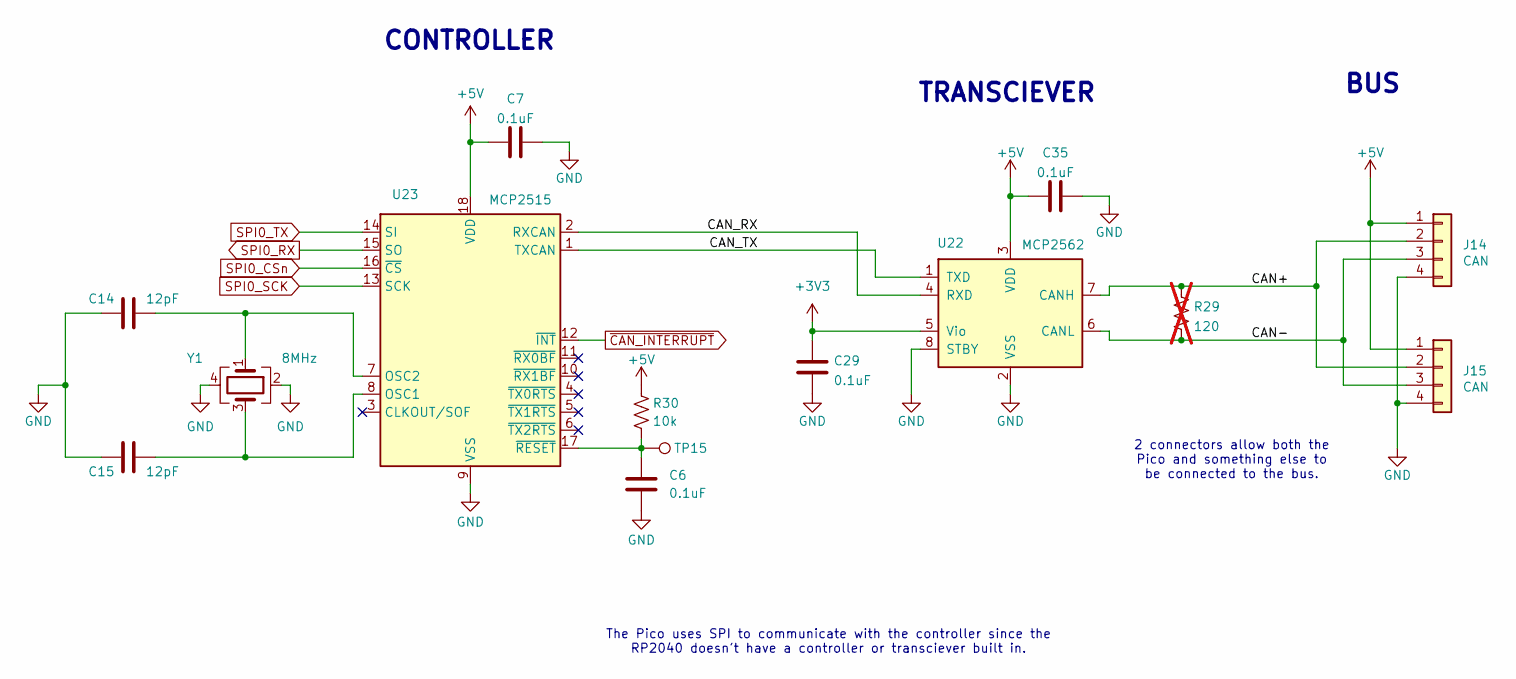
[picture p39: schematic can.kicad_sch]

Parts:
C6, C7, C29, C35: 0.1uF; C_1206_3216Metric_Pad1.33x1.80mm_HandSolder; Manufacturer Part Number C1206C104J5RACTU
C14, C15: 12pF; C_0603_1608Metric_Pad1.08x0.95mm_HandSolder; Manufacturer Part Number C0603C120K5RACTU
J14, J15: CAN; Molex_PicoBlade_53047-0410_1x04_P1.25mm_Vertical; Manufacturer Part Number 0530470410
R29: 120; R_0603_1608Metric_Pad0.98x0.95mm_HandSolder; Manufacturer Part Number RNCP0603FTD121R; not fitted
R30: 10k; R_0603_1608Metric_Pad0.98x0.95mm_HandSolder; Manufacturer Part Number RNCP0603FTD10K0
TP15: ~{RST}; TestPoint_Pad_D1.0mm
U22: MCP2562; SOIC-8_3.9x4.9mm_P1.27mm; Manufacturer Part Number MCP2562FDT-E/SN
U23: MCP2515; SOIC-18W_7.5x11.6mm_P1.27mm; Manufacturer Part Number MCP2515T-E/SO
Y1: 8MHz; Crystal_SMD_3225-4Pin_3.2x2.5mm; Manufacturer Part Number FL0800011Q

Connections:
+3V3: C29.1, U22.5 (Vio); also elsewhere on the board
+5V: C7.1, C35.1, J14.1, J15.1, R30.2, U22.3 (VDD), U23.18 (VDD); also elsewhere on the board
/CAN/CAN+: J14.2, J15.2, R29.2, U22.7 (CANH)
/CAN/CAN-: J14.3, J15.3, R29.1, U22.6 (CANL)
/CAN/CAN_RX: U22.4 (RXD), U23.2 (RXCAN)
/CAN/CAN_TX: U22.1 (TXD), U23.1 (TXCAN)
GND: C6.2, C7.2, C14.1, C15.1, C29.2, C35.2, J14.4, J15.4, U22.2 (VSS), U22.8 (STBY), U23.9 (VSS), Y1.2, Y1.4; also elsewhere on the board
unnamed: C15.2, U23.8 (OSC1), Y1.3
unnamed: C14.2, U23.7 (OSC2), Y1.1
unnamed: C6.1, R30.1, TP15.1, U23.17 (~RESET)
SPI0_CSn: U23.16 (~CS); also elsewhere on the board
SPI0_RX: U23.15 (SO); also elsewhere on the board
SPI0_SCK: U23.13 (SCK); also elsewhere on the board
SPI0_TX: U23.14 (SI); also elsewhere on the board
~CAN_INTERRUPT: U23.12 (~INT); also elsewhere on the board

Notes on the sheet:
The Pico uses SPI to communicate with the controller since the RP2040 doesn't have a controller or transciever built in.
2 connectors allow both the Pico and something else to be connected to the bus.
CONTROLLER
BUS
TRANSCIEVER

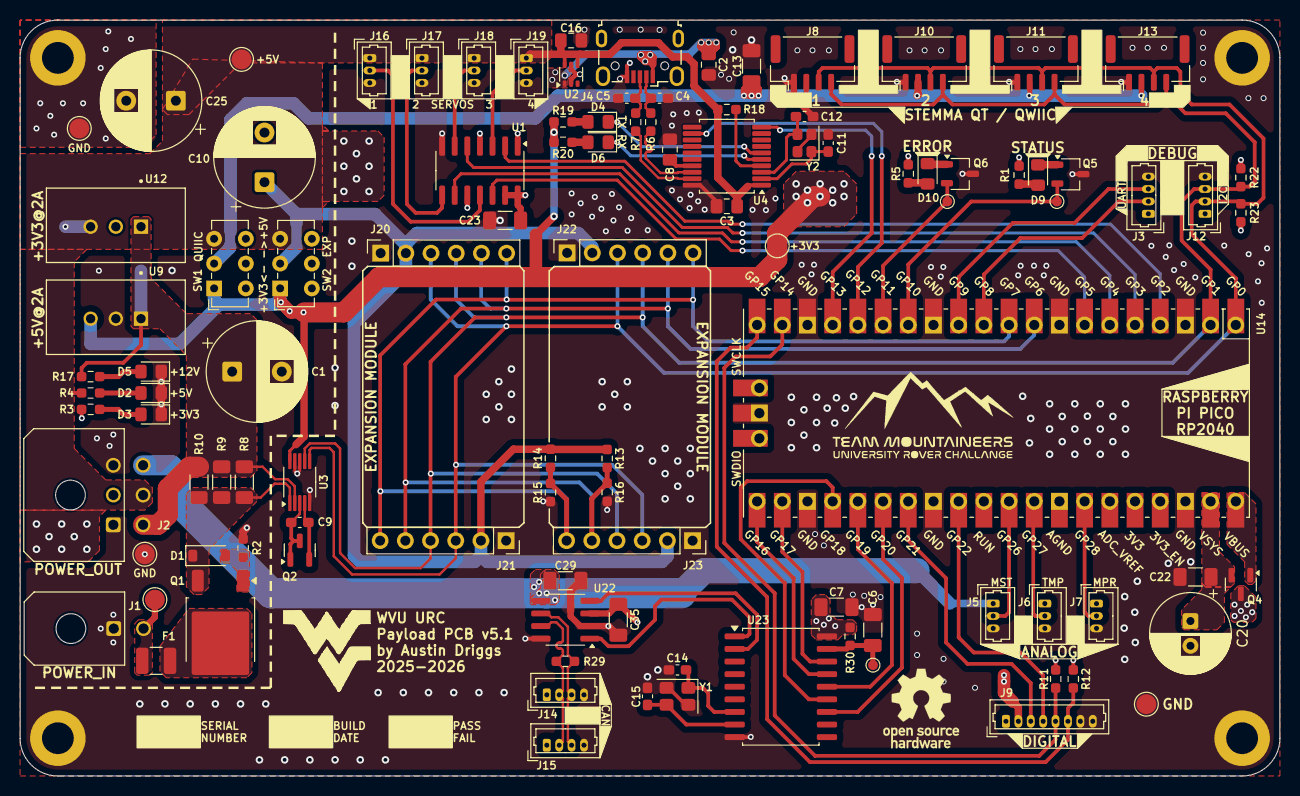
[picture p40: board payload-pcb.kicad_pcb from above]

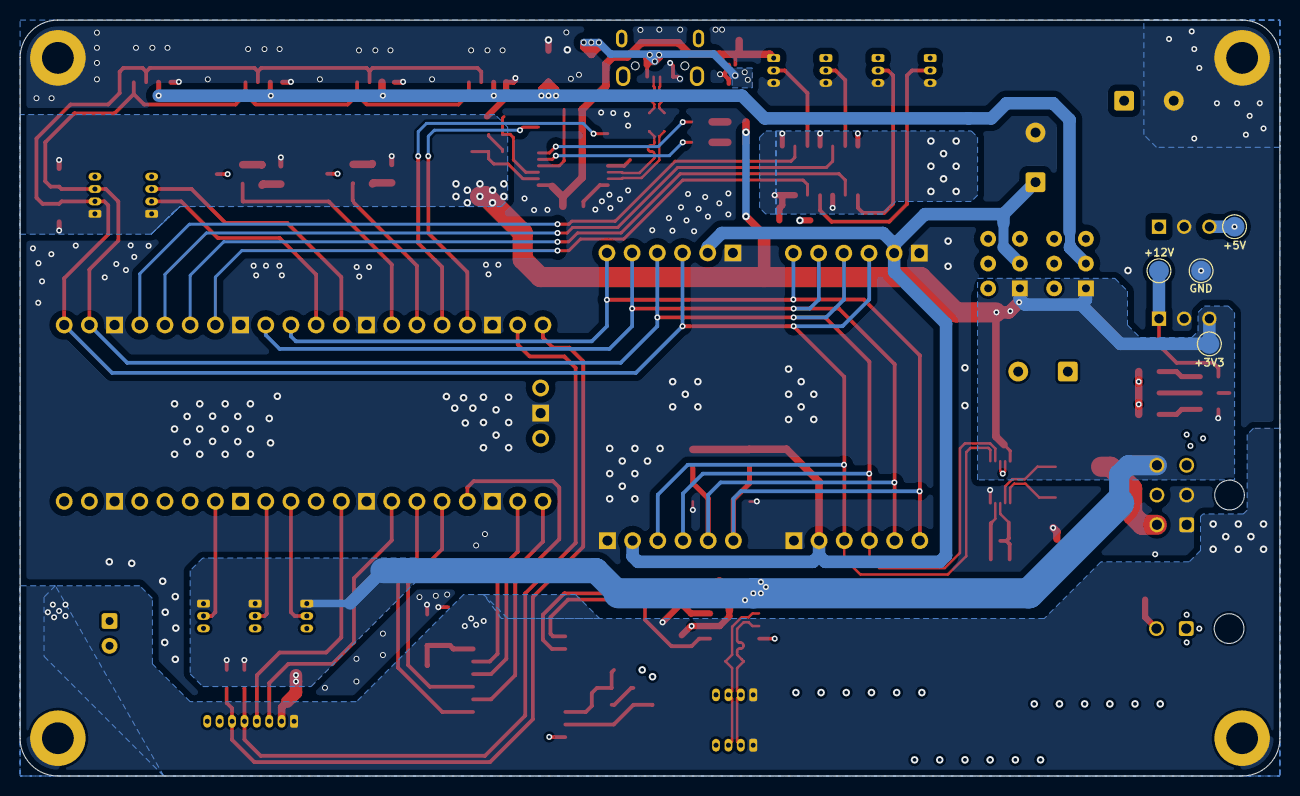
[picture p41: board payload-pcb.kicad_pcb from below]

Board: 4 copper layers, 127.0 x 76.2 mm, 113 parts (4 on the bottom side), 71 nets.

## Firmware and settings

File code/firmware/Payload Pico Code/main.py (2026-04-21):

# ==========================================
# SCIENCE MODULE (FINAL STABLE) Combo Science Works with topic echoing on ros
# ==========================================

import machine
from machine import Pin, I2C, PWM
from bme680 import BME680_I2C
import time
import sys
import select


# ==========================================
# INITIALIZATION
# ==========================================

def init():

    # I2C SETUP (with proper delay + scan)
    try:
        i2c = I2C(0, sda=Pin(0), scl=Pin(1), freq=100000)
        time.sleep(0.3)

        # Retry scan (handles slow sensor boot)
        devices = []
        for _ in range(5):
            devices = i2c.scan()
            if devices:
                break
            time.sleep(0.2)

    except:
        i2c = None
        devices = []

    # SENSOR INIT (only if detected)
    bme1 = None
    bme2 = None

    if i2c:
        if 0x76 in devices:
            try:
                bme1 = BME680_I2C(i2c, address=0x76)
            except:
                bme1 = None

        if 0x77 in devices:
            try:
                bme2 = BME680_I2C(i2c, address=0x77)
            except:
                bme2 = None

    # RELAYS
    halogen = Pin(21, Pin.OUT)
    halogen.value(0)

    # LIMIT SWITCHES
    limit_switch_1 = Pin(14, Pin.IN, Pin.PULL_UP)
    limit_switch_2 = Pin(15, Pin.IN, Pin.PULL_UP)

    # ACTUATOR PWM
    actuator_pwm = PWM(Pin(4))
    actuator_pwm.freq(50)
    actuator_pwm.duty_u16(int(65535 * 0.075))  # neutral

    # COMMAND INPUT
    poller = select.poll()
    poller.register(sys.stdin, select.POLLIN)

    return {
        "bme1": bme1,
        "bme2": bme2,
        "halogen": halogen,
        "actuator_pwm": actuator_pwm,
        "limit_switch_1": limit_switch_1,
        "limit_switch_2": limit_switch_2,
        "poller": poller
    }


# ==========================================
# SAFE SENSOR READ
# ==========================================

def read_bme(sensor):
    if sensor:
        try:
            time.sleep(0.05)
            return (
                sensor.temperature,
                sensor.pressure,
                sensor.humidity
            )
        except:
            return (0.0, 0.0, 0.0)
    return (0.0, 0.0, 0.0)


# ==========================================
# MAIN LOOP
# ==========================================

def run():

    state = init()

    bme1 = state["bme1"]
    bme2 = state["bme2"]
    halogen = state["halogen"]
    actuator = state["actuator_pwm"]
    limit_switch_1 = state["limit_switch_1"]
    limit_switch_2 = state["limit_switch_2"]
    poller = state["poller"]

    STREAM_INTERVAL_MS = 100
    last_stream = time.ticks_ms()

    while True:

        # ---- STREAM ----
        if time.ticks_diff(time.ticks_ms(), last_stream) >= STREAM_INTERVAL_MS:

            t1, p1, h1 = read_bme(bme1)
            t2, p2, h2 = read_bme(bme2)

            lim1 = 0 if limit_switch_1.value() else 1
            lim2 = 0 if limit_switch_2.value() else 1

            print("{:.6f},{:.6f},{:.6f},{:.6f},{:.6f},{:.6f},{},{}".format(
                t1, p1, h1,
                t2, p2, h2,
                lim1, lim2
            ))

            last_stream = time.ticks_ms()

        # ---- COMMANDS ----
        if poller.poll(0):
            cmd = sys.stdin.readline().strip()

            if cmd == "hbon":
                halogen.value(1)

            elif cmd == "hboff":
                halogen.value(0)

            elif cmd == "reset":
                machine.reset()

            elif cmd == "act_extend":
                actuator.duty_u16(int(65535 * 0.10))

            elif cmd == "act_retract":
                actuator.duty_u16(int(65535 * 0.05))

            elif cmd == "act_stop":
                actuator.duty_u16(int(65535 * 0.075))

        time.sleep(0.01)

run()

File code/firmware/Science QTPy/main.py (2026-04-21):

from machine import Pin, I2C
import onewire
import ds18x20
import time
import sys
import select

# -------------------------
# ACTUATOR SETUP
# -------------------------

IN1 = Pin(4, Pin.OUT)
IN2 = Pin(6, Pin.OUT)
EN1 = Pin(5, Pin.OUT)

def stop():
    EN1.value(0)
    IN1.value(0)
    IN2.value(0)

def retract():
    EN1.value(1)
    IN1.value(1)
    IN2.value(0)

def extend():
    EN1.value(1)
    IN1.value(0)
    IN2.value(1)

# Start OFF
stop()

# -------------------------
# Soil Moisture Sensor (I2C1)
# -------------------------

i2c = I2C(1, sda=Pin(22), scl=Pin(23), freq=100000)
soil_addr = 0x28

print("I2C scan:", i2c.scan())

# -------------------------
# DS18B20 Temperature
# -------------------------

dat = Pin(26)
ow = onewire.OneWire(dat)
ds = ds18x20.DS18X20(ow)

roms = ds.scan()
print("Temp sensor ROM:", roms)

# -------------------------
# Non-blocking serial check
# -------------------------

def read_command():
    if sys.stdin in select.select([sys.stdin], [], [], 0)[0]:
        cmd = sys.stdin.readline().strip()
        return cmd
    return None

# -------------------------
# Main loop
# -------------------------

while True:

    # ---- Check for command ----
    cmd = read_command()
    if cmd:
        print("CMD:", cmd)

        if cmd == "extend":
            extend()
        elif cmd == "retract":
            retract()
        elif cmd == "stop":
            stop()
        else:
            print("Unknown command")

    # ---- Temperature ----
    ds.convert_temp()
    time.sleep(1)

    temp = None
    for rom in roms:
        temp = round(ds.read_temp(rom), 2)

    # ---- Moisture ----
    moisture = None
    try:
        data = i2c.readfrom_mem(soil_addr, 0x05, 2)
        moisture = data[1] << 8 | data[0]
    except:
        print("Moisture sensor read error")

    # ---- Print results ----
    print(f"{moisture}, {temp}")

    time.sleep(1)

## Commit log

2025-10-07 payload pcb v1.0
    [173010342_STP_173010342_rev1.stp, 430450400.stp, 768250002.stp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]
2025-10-07 payload pcb v2.0
    [173010342_STP_173010342_rev1.stp, 430450200.stp, 430450400.stp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]
2025-10-07 payload pcb v3.0
    [39301062.stp, 393570002.stp, 469911024.stp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]
2025-10-07 payload pcb v3.1
    [050362296.stp, 1050170001.stp, 2604-1102.stp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]
2025-11-13 initial cleanup of repo
    [Payload_PCB_v3.1-B_Cu.gbl, Payload_PCB_v3.1-B_Mask.gbs, Payload_PCB_v3.1-B_Paste.gbp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]
2025-12-03 major, major rework for v5.0 and pdr
    [Payload_PCB_v3.1.kicad_pcb, Payload_PCB_v3.1.kicad_sch, can.kicad_sch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]
2025-12-03 more cleanup and added notes for review
    [can.kicad_sch, gpio.kicad_sch, leds.kicad_sch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]
2025-12-03 DNP unused connectors for now
    [can.kicad_sch, gpio.kicad_sch, leds.kicad_sch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]
2025-12-03 pcb review session notes
    [gpio.kicad_sch, leds.kicad_sch, payload-pcb.kicad_pcb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]
2025-12-04 major rework again after the meeting
    [430450200.stp, 430450602.stp, 530470310.stp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]
2026-01-03 major finishing touches: - major rework for v5.1 - silkscreen and stuff - impednace for USB and CAN lines - schematic comments - symbol, footprint, and model library updates
    [050362296.stp, 1050170001.stp, 173010342_STP_173010342_rev1.stp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]
2026-01-03 removed unnecessary files
    [leds.kicad_sch]
2026-01-03 moved gerbers to releases
    [payload-pcb-B_Cu.gbl, payload-pcb-B_Mask.gbs, payload-pcb-B_Paste.gbp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]
2026-01-03 some repo cleanup
    [pico.kicad_sch]
2026-01-03 some more docs. updated pico VPN to CT
    [can.kicad_sch, gpio.kicad_sch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]
2026-01-03 generated gerbers for v5.1
    [payload-pcb-B_Cu.gbl, payload-pcb-B_Mask.gbs, payload-pcb-B_Paste.gbp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]
2026-01-03 swapped UART to USB from FTDI (out of stock) to MCP2200
    [can.kicad_sch, gpio.kicad_sch, payload-pcb-v5.1-bom.csv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]
2026-01-03 added release documents for v5.1 (pending approval)
    [2026-01-03T141116.csv, 2026-01-03T141116.xlsx, 2026-01-03T141637.csv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]
2026-01-11 touch ups from peer reviews
    [can.kicad_sch, gpio.kicad_sch, payload-pcb.kicad_pcb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]
2026-01-13 updated some release files for v5.1
    [2026-01-03T141116.csv, 2026-01-03T141116.xlsx, 2026-01-03T141637.csv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]
2026-01-13 updated rest of release files
    [payload-pcb-B_Cu.gbl, payload-pcb-B_Fab.gbr, payload-pcb-B_Mask.gbs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]
2026-01-13 updated assembly pdf page names
2026-01-13 updated release files, bom, and jlc file
    [2026-01-03T141637.csv, 2026-01-03T141637.xlsx, payload-pcb-v5.1-bom.csv]
2026-01-16 Added housing/cable/header info to each connector's symbol properties.
    [can.kicad_sch, gpio.kicad_sch, payload-pcb.kicad_sch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]
2026-01-16 Imported connector info to PCB layout.
    [payload-pcb.kicad_pcb]
2026-01-16 Updated net class grouping and colors.
    [can.kicad_sch, gpio.kicad_sch, payload-pcb.kicad_pcb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]
2026-01-16 schematic cleanup
    [payload-pcb.kicad_pcb, payload-pcb.kicad_sch, power.kicad_sch]
2026-05-08 backup of refs from laptop on 2026-04-08
    [flying_wv.stl]

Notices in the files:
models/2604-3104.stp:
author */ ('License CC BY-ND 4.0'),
